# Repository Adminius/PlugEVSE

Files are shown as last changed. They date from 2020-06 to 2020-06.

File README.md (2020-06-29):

# PlugEVSE
Mit PlugEVSE kann man ein Elektroauto aufladen. 
Vorteil ist, dass die komplette Elektronik (außer Fehlerstromschutzschalter) direkt im Type 2 Stecker verbaut ist.
PlugEVSE basiert auf dem Schaltplan von AnalogEVSE: http://www.analogevse.xyz/ 
Viele Informationen, z.B. Funktionsweise und Troubleshooting können der Seite entnommen werden.
Die größte Änderung im Vergleich zu AnalogEVSE ist die Umstellung auf SMD Bauteile um Platz zu sparen. Zusätzlich wurden Relais und Netzteil "ausgelagert".

## Was kann PlugEVSE:
- Laden mit fest eingestellter Stromstärke, z.B. mit 16A oder 32A (andere Werte sind möglich)

## Was kann PlugEVSE nicht:
- Erdungsüberwachung. Deswegen ist empfohlen PlugEVSE nur an geprüftem Anschluss mit funktionierender Erdung zu nutzen
- Es wird eine Fehlerstromschutzschalter Typ A EV oder Typ B vorausgesetzt. 

# ACHTUNG
- Wenn Begrife "Erdung" oder "Fehlerstromschutzschalter" nicht bekannt sind, dann ist dieses Projekt nichts für Sie! Sorry!
- Beim Zusammenbau wird mit **lebensgefährlicher** Netzspannung gearbeitet!
- Die Nutzung erfolgt auf eigene Gefahr. Ich übernehme keine Haftung!

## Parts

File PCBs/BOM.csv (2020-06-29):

Part | Desc | Long Desc | Case | Manuf. Partnr. | Mouser | Comment
D1 | Z-Diode | 2.4V | SOD-123 | MMSZ4681-E3-08 | 78-MMSZ4681-E3-08
D2 | Z-Diode | 7.5V | SOD-123 | MMSZ5236B-E3-08 | 78-MMSZ5236B-E3-08
D3,D4,D5,D6 | Diode | 1N4148 | SOD-123 | 1N4148W-7-F | 621-1N4148W-F
V1 | DC-DC | Isol. DC-DC 12V |  | CRE1S1212SC | 580-CRE1S1212SC
IC2,IC3 | IC | LM2901 | SOIC-14 D | LM2901DRG3 | 595-LM2901DRG3
IC1 | IC | CD4060B | SO-16 | CD4060BNSR | 595-CD4060BNSR
Y2 | 8.192 MHz | 8.192 MHz Resonator |  | CSTNE8M19G550000R0 | 81-CSTNE8M19G550000R | Alt: Y1+C4,C5
Y1 | 4.096 MHz | 4.096 MHz Resonator |  | ABLS-4.096MHz-D-3-Y-T | 815-ABLS4096MHZD3YT
T1,T3 | NPN | NPN Transistor | SOT23 | BC817K-40HR | 771-BC817K-40HR
T2 | PNP | PNP Transistor | SOT23 | BC857B,215 | 771-BC857B-T/R
R10 | Trimm-R |  | 3mm | TC33X-1-473E | 652-TC33X-1-473E | current selection
R1,R6,R7,R8 | 2K2 0603 |  | 0603
R22 | 3K3 0603 |  | 0603
R2,R5 | 4K7 0603 |  | 0603
R3 | 5K6 0603 |  | 0603
R16 | 1K 0603 |  | 0603
R4,R9,R13,R14,R15,R17,R21 | 10K 0603 |  | 0603
R19,R20 | 1M 0603 |  | 0603
R11,R12 | 51K 0603 |  | 0603 |  |  | current selection
R11,R12 | 56K 0603 |  | 0603 |  |  | current selection
R12 | 33K 0603 |  | 0603 |  |  | current selection
R18 | 220/680R | 220/680R 1W 2512 | 2512 |  |  | optional, PP-resistor
C1 | 10uF | 10uF 3216 Tantalum | 3216
C2,C6,C7,C8,C9 | 100n |  | 0603
C3 | 1uF |  | 0603
C4,C5 | 22pF |  | 0603 |  |  | only for Y1
C10 | 47uF | 47uF Radial Cap. | 5mm | 860010372004 | 710-860010372004
LED | RGB LED | RGB LED | 5mm | HV-5RGB60 | 743-HV-5RGB60
Relais 23A | 23A Relais |  |  | G2RL-1A-E2-CV-HA DC12 | 653-G2RL1AE2CVHADC12
Relais 36A | 36A Relais |  |  | G6QE-1A DC12 | 653-G6QE-1ADC12
Type 2 Plug |  |  |  | DUOSIDA |  | 20A or 32A version, single phase

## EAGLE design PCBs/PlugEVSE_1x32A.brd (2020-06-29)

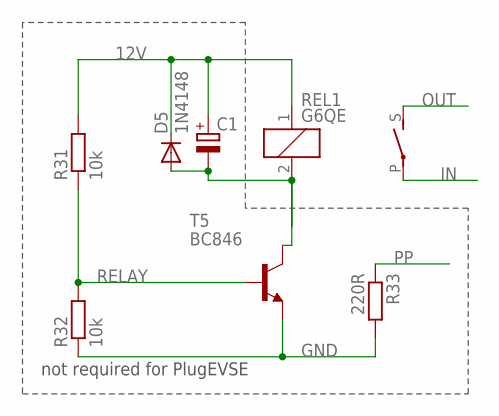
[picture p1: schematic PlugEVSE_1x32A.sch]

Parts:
C1: CPOL-EUSMCC; SMC_C
D5: 1N4148; SOD123
R31, R32: 10k; R0603
R33: 220R; R2512
REL1: G6QE
T5: BC846; SOT23

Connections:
12V: C1.+, D5.C, R31.2, REL1.1
GND: R32.1, R33.2, T5.2 (E)
IN: REL1.P
OUT: REL1.S
PP: R33.1
RELAY: R31.1, R32.2, T5.1 (B)
RL: C1.-, D5.A, REL1.2, T5.3 (C)

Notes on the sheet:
not required for PlugEVSE

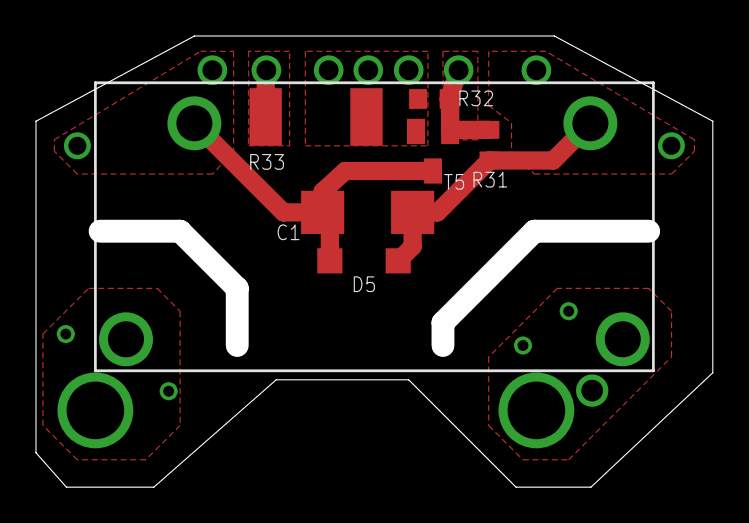
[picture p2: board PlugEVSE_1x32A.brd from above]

Board: 2 copper layers, 37.6 x 25.1 mm, 7 parts (0 on the bottom side), 4 nets.

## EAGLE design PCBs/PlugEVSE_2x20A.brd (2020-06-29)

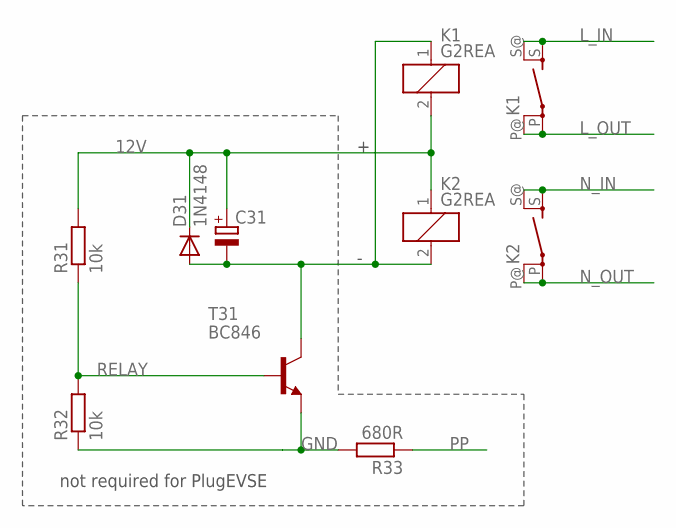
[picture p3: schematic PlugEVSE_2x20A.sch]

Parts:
C31: CPOL-EUSMCC; SMC_C
D31: 1N4148; SOD123
K1, K2: G2REA
R31, R32: 10k; R0603
R33: 680R; R2512
T31: BC846; SOT23

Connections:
12V: C31.+, D31.C, K1.2, K2.1, R31.2
GND: R32.1, R33.2, T31.2 (E)
L_IN: K1.S, K1.S@ (S)
L_OUT: K1.P, K1.P@
N_IN: K2.S, K2.S@ (S)
N_OUT: K2.P, K2.P@
PP: R33.1
RELAY: R31.1, R32.2, T31.1 (B)
RL: C31.-, D31.A, K1.1, K2.2, T31.3 (C)

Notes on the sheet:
not required for PlugEVSE

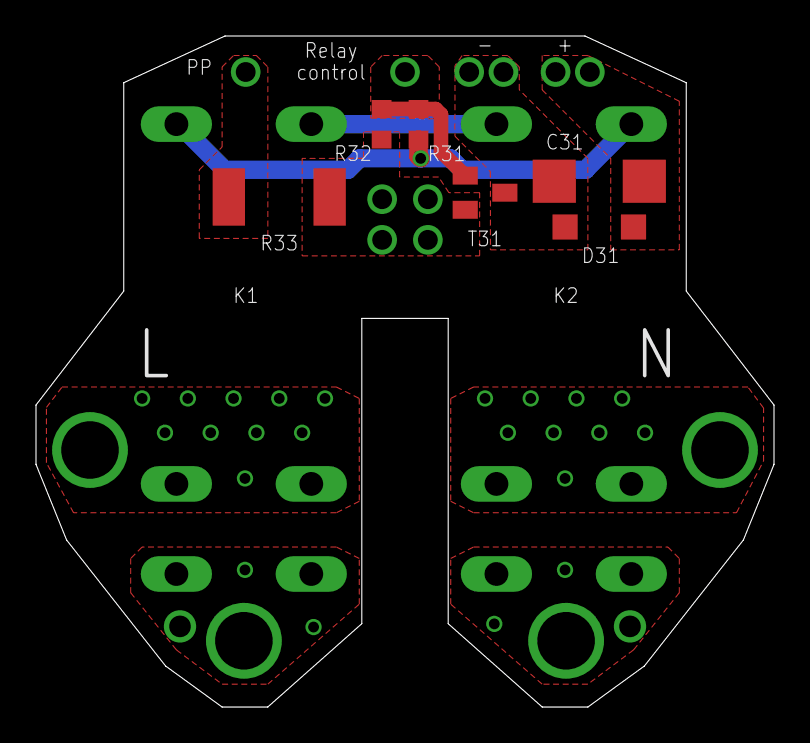
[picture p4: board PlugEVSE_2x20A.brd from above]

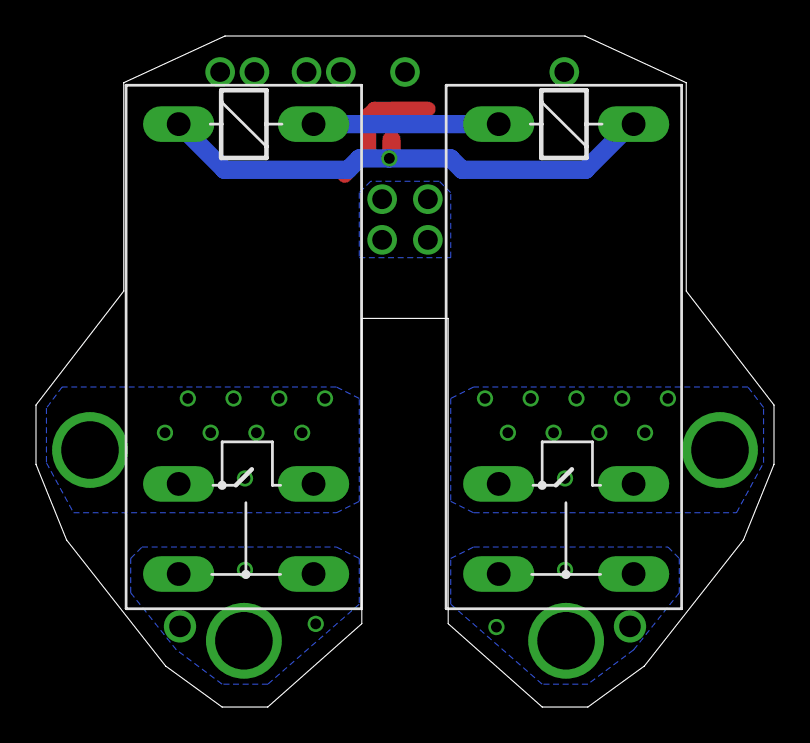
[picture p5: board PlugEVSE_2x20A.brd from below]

Board: 2 copper layers, 41.0 x 37.3 mm, 8 parts (2 on the bottom side), 8 nets.

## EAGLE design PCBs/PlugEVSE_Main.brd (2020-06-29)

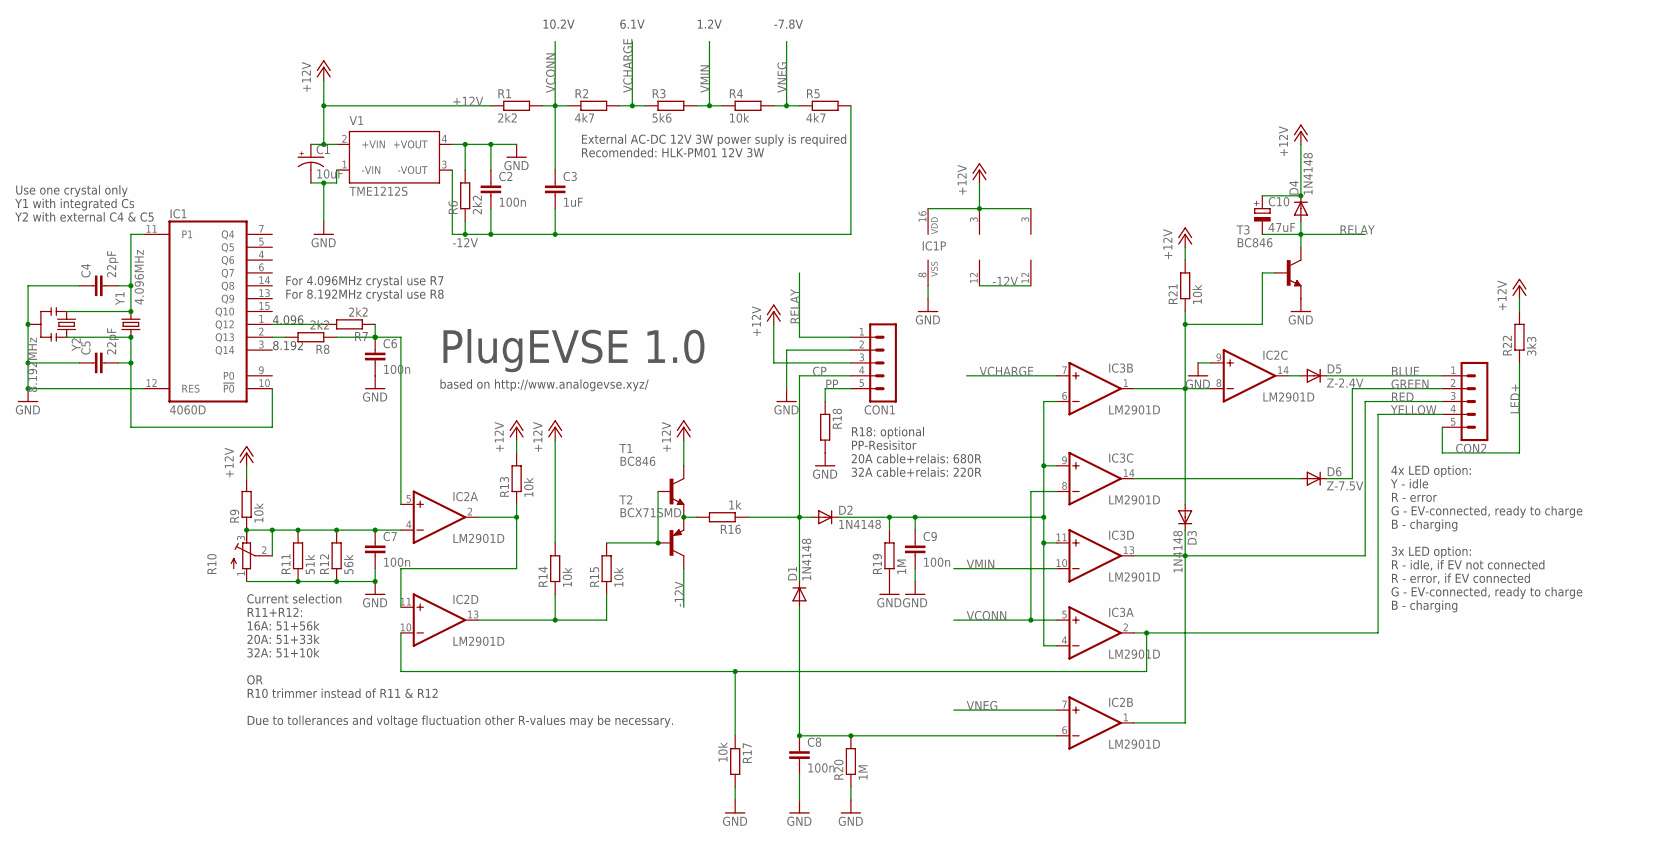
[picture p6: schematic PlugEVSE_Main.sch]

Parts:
C1: 10uF; EIA3216
C2, C6, C7, C8, C9: 100n; C0603
C3: 1uF; C0603
C4, C5: 22pF; C0603
C10: 47uF; E2,5-5
CON1, CON2: MA05-1
D1, D2, D3, D4: 1N4148; SOD123
D5: Z-2.4V; SOD123
D6: Z-7.5V; SOD123
IC1: 4060D; SO16
IC2, IC3: LM2901D; SO14
R1, R6, R7, R8: 2k2; R0603
R2, R5: 4k7; R0603
R3: 5k6; R0603
R4, R9, R13, R14, R15, R17, R21: 10k; R0603
R10: R-TRIMM3202; RTRIM3202
R11: 51k; R0603
R12: 56k; R0603
R16: 1k; R0603
R18: R-EU_R2512; R2512
R19, R20: 1M; R0603
R22: 3k3; R0603
T1, T3: BC846; SOT23
T2: BCX71SMD; SOT23
V1: TME1212S; TME
Y1: 4.096MHz; 11.4X4.5
Y2: 8.192MHz; RESONATOR-SMD

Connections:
+12V: C1.A (+), C10.+, CON1.3, D4.C, IC1.16 (VDD), IC2.3 (V+), IC3.3 (V+), R1.1, R9.2, R13.2, R14.2, R21.2, R22.2, T1.3 (C), V1.2 (+VIN)
-12V: C2.2, C3.2, IC2.12 (V-), IC3.12 (V-), R5.2, R6.1, T2.3 (C), V1.3 (-VOUT)
BLUE: CON2.1, D5.C
CP: CON1.4, D1.C, D2.A, R16.1
GND: C1.C (-), C2.1, C4.1, C5.1, C6.2, C7.2, C8.2, C9.2, CON1.2, IC1.8 (VSS), IC1.12 (RES), IC2.9 (+IN), R6.2, R10.1 (A), R11.1, R12.1, R17.2, R18.2, R19.1, R20.1, T3.2 (E), V1.1 (-VIN), V1.4 (+VOUT), Y2.2
GREEN: CON2.2, D6.C
LED+: CON2.5, R22.1
unnamed: R16.2, T1.2 (E), T2.2 (E)
unnamed: IC1.2 (Q13), R8.2
unnamed: IC1.1 (Q12), R7.2
unnamed: C6.1, IC2.5 (+IN), R7.1, R8.1
unnamed: IC2.13 (OUT), R14.1, R15.1
unnamed: C8.1, D1.A, IC2.6 (-IN), R20.2
unnamed: C9.1, D2.C, IC3.4 (-IN), IC3.6 (-IN), IC3.9 (+IN), IC3.11 (+IN), R19.2
unnamed: D3.A, IC2.8 (-IN), IC3.1 (OUT), R21.1, T3.1 (B)
unnamed: C7.1, IC2.4 (-IN), R9.1, R10.2 (S), R10.3 (E), R11.2, R12.2
unnamed: IC2.2 (OUT), IC2.11 (+IN), R13.1
unnamed: R15.2, T1.1 (B), T2.1 (B)
unnamed: C4.2, IC1.11 (P1), Y1.2, Y2.1
unnamed: D5.A, IC2.14 (OUT)
unnamed: D6.A, IC3.14 (OUT)
unnamed: C5.2, IC1.10 (!P0), Y1.1, Y2.3
PP: CON1.5, R18.1
RED: CON2.3, D3.C, IC2.1 (OUT), IC3.13 (OUT)
RELAY: C10.-, CON1.1, D4.A, T3.3 (C)
VCHARGE: IC3.7 (+IN), R2.2, R3.1
VCONN: C3.1, IC3.5 (+IN), IC3.8 (-IN), R1.2, R2.1
VMIN: IC3.10 (-IN), R3.2, R4.1
VNEG: IC2.7 (+IN), R4.2, R5.1
YELLOW: CON2.4, IC2.10 (-IN), IC3.2 (OUT), R17.1

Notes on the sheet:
10.2V
6.1V
1.2V
-7.8V
8.192
4.096
Current selection R11+R12: 16A: 51+56k 20A: 51+33k 32A: 51+10k OR R10 trimmer instead of R11 & R12 Due to tollerances and voltage fluctuation other R-values may be necessary.
Use one crystal only Y1 with integrated Cs Y2 with external C4 & C5
For 4.096MHz crystal use R7 For 8.192MHz crystal use R8
4x LED option: Y - idle R - error G - EV-connected, ready to charge B - charging 3x LED option: R - idle, if EV not connected R - error, if EV connected G - EV-connected, ready to charge B - charging
PlugEVSE 1.0
based on http://www.analogevse.xyz/
R18: optional PP-Resisitor 20A cable+relais: 680R 32A cable+relais: 220R
External AC-DC 12V 3W power suply is required Recomended: HLK-PM01 12V 3W

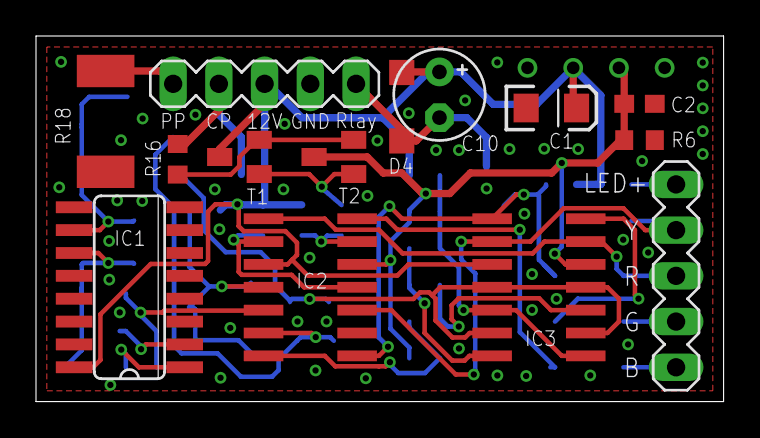
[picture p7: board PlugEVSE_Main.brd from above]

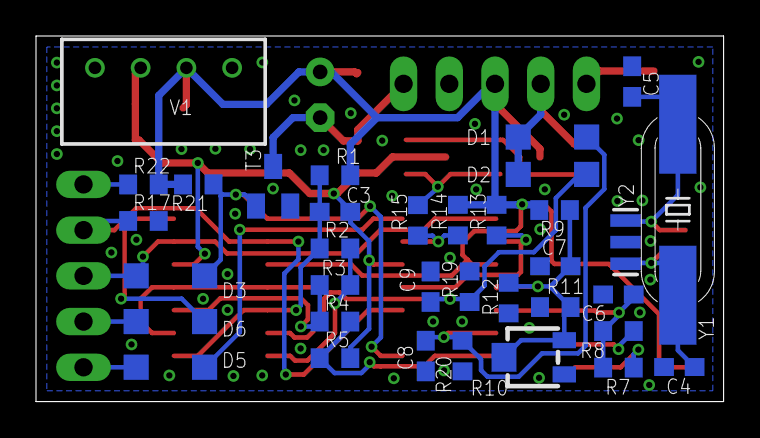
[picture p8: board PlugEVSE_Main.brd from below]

Board: 2 copper layers, 38.2 x 20.3 mm, 49 parts (35 on the bottom side), 30 nets.

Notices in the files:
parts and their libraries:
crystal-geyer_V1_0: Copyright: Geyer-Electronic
